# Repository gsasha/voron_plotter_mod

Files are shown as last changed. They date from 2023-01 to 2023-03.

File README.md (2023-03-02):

## Voron SB Plotter mod

###### Printing:
- Default voron settings, correct orientation
- No supports needed

###### Bom:
- 7 M3x8
- 7 M3 heatset inserts
- A very long M3 screw - including a long smooth part. 80mm is a good variant.
- A long spring. One harvested from a pen will be fine.
- 2 M3 washers
- MGW12C 100mm linear slide. Any other slide can be used, it's just one that was at hand.
- Sharpie pen.
- Vinyl cutter knife.

###### Description:
This is a plotter extension for Voron StealthBurner.
It uses a modified SB main body that includes two additional heatset inserts that the plotter attachment can be screwed to and removed easily.

The STLs supplied are tuned for MGW12C linear slide and regular Sharpie pen. However, most any slide and any pen can be used - LMK if you want STLs for different linear slides.

###### Assembly:

There are three printed parts: modified SB body, mounted plate and pen holder.

1. Print all the parts normally. The pen holder can be placed upside-down, this way it can be printed without supports. Otherwise, only the tab needs to be printed.

2. Install heatsets as indicated.
Pay especial attention to the plate - it is very important for alignment that the inserts are flush or even a bit deep.

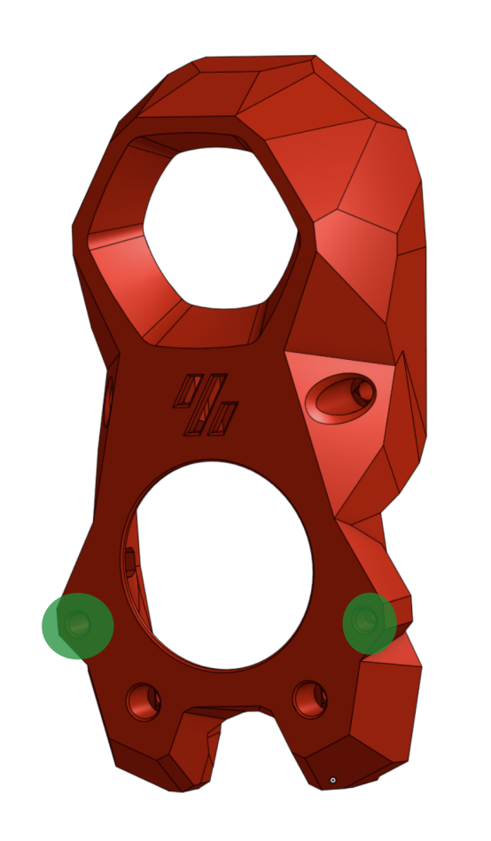
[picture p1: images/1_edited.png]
SB body
,
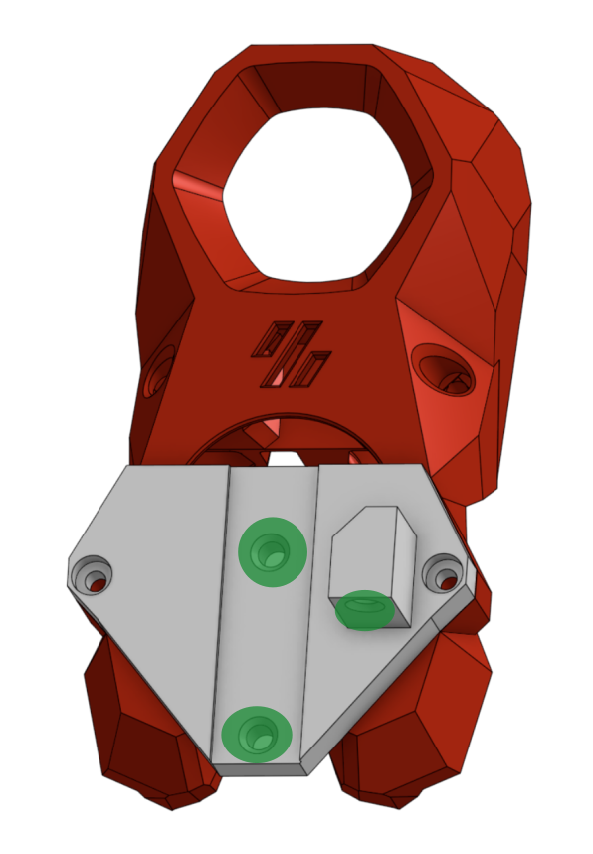
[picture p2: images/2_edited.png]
Plate
,
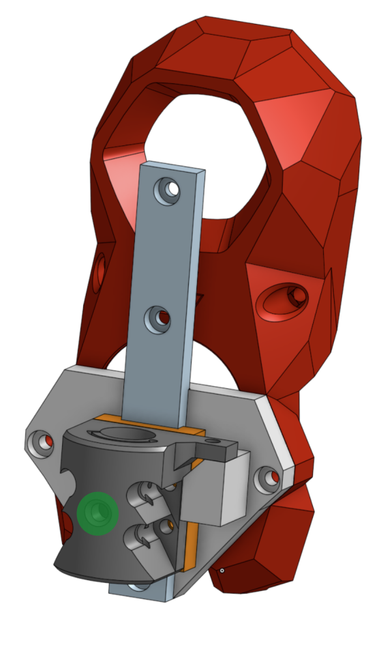
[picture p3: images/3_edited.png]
Pen Holder
.

3. Install the SB body onto the printer. The rest of the mechanism can be connected to it and disconnected again at will.

4. Screw the linear slide to the plate.

5. Screw the pen holder to the block.

6. Put a washer, a spring and another washer onto the long screw and screw it in from the top into the heatset insert on the limiter.

7. Insert a screw into the heatset in the pen holder.

###### Changing printer.cfg
Include the provider plot.cfg. Modify according to your printer (see comments inside).

###### Preparing Plotter file:

Plotter file must include `PLOT_START` as starter command.
For inkscape, copy the "inkscape/header" and "inkscape/footer" files to the directory where you put the output file.

Run the gcode through inkscape/preprocess.py to make it acceptable by klipper.

###### Running:

:warning: **!!!!! IMPORTANT !!!!!!** To prevent head crash, run the plotter with printer doors open.

Install the adapter (but not the pen) on the head. Run your generated gcode file.

The head should run the homing sequence and stop in the air. Install the pen so that it touches the bed, attach a page to be plotted using masking tape and unpause the printer.

##### Changelog:

**2 Mar 2023**:

- Added support for cutter knife.
- Knife and pen adapters are now interchangeable with less disassembly. In particular, the bolt holding the screw does not need to be removed.
- Small improvements to the structure to make it easier to print.
- Added location for nuts that can store mounting screws.

Enjoy!

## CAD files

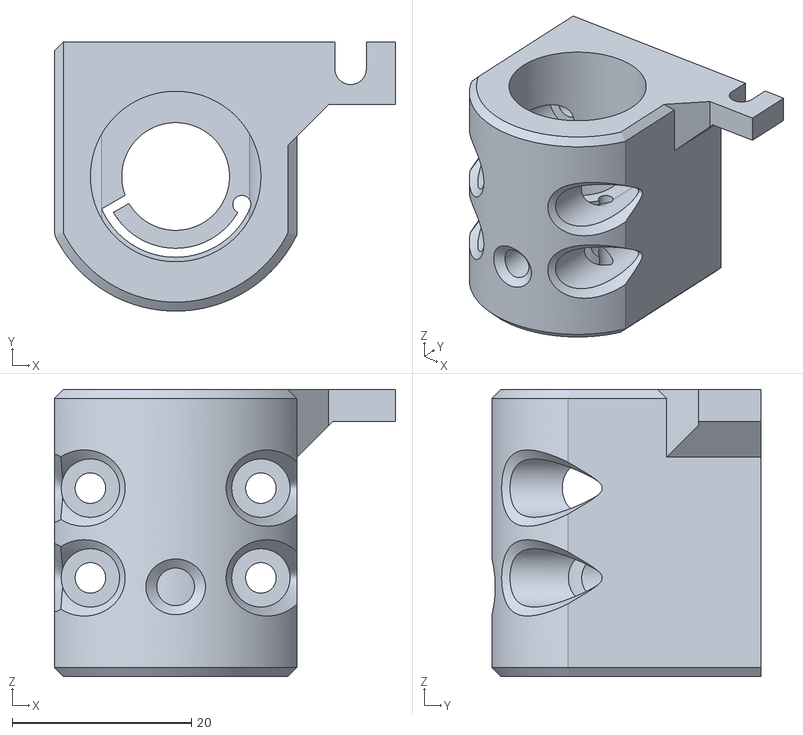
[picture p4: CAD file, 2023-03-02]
STL/mgw12c_holder_sharpie.stl
38.0 x 30.0 x 32.0

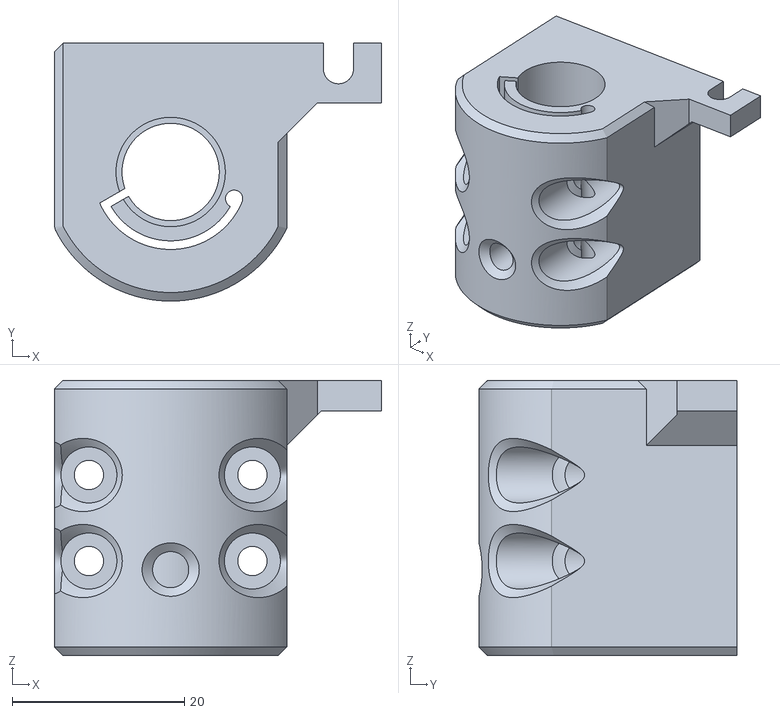
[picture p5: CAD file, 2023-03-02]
STL/mgw12c_holder_cutter.stl
38.0 x 30.0 x 32.0

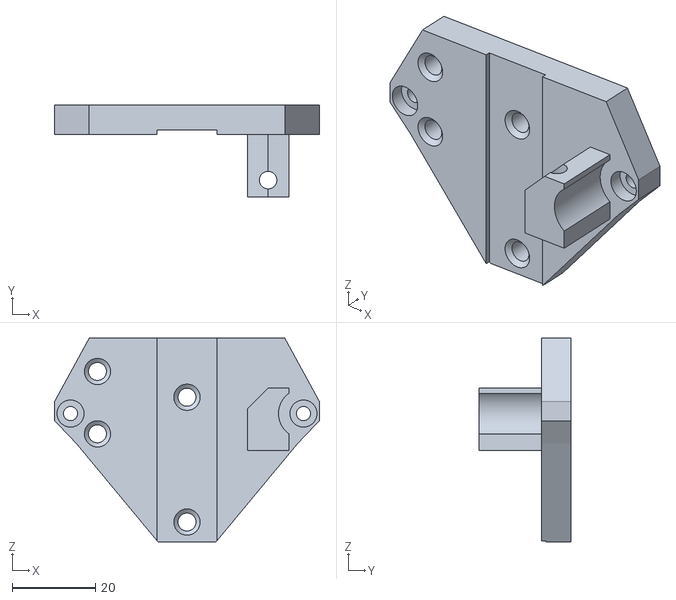
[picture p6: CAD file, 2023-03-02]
STL/mgw12c_plate.stl
63.7 x 22.0 x 48.9

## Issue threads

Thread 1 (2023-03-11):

On top of normal Stealthburner

14roiron, 2023-03-11:
Hello
Instead of reprinting a stealbruner top, I tried to modify your holder to be closer to the real one
I merged it with this one
https://github.com/DrPacemaker/Voron-Laser-Mod
but then support are required to print it, so it is not ideal
[plotter v1.stl.zip](https://github.com/gsasha/voron_plotter_mod/files/10948012/plotter.v1.stl.zip)

gsasha, 2023-03-12:
Nice!

Initially I tried this style of mount, but I decided that I don't like the
idea of disassembling the existing screws holding the SB faceplate.
Both have a right to exist, and I think we can try to make the mounts
compatible. WDYT?

An alternative way I'm thinking to implement this is to use a longer screw
permanently mounted in SB head with an adapter like this mounted on top of
it:
https://www.aliexpress.com/item/1005004157933737.html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,scm-url:1007.40050.281175.0,pvid:a579ff90-30bd-4b7a-bcaf-5242bfad5005,tpp_buckets:668%232846%238112%231997&isseo=y&pdp_ext_f=%7B%22sku_id%22%3A%2212000028233431605%22%2C%22sceneId%22%3A%2230050%22%7D&pdp_npi=3%40dis%21USD%213.0%212.82%21%21%21%21%21%40211b600e16786112126063788ea394%2112000028233431605%21rec%21IL%21171720285

Then, you can attach your extension to the adapter using a M5 nut. This is
not as fun as using an allen key, but still would be something that you can
attach to SB head without unscrewing it each time.

In the perfect world, we could find a stud like this:
https://www.aliexpress.com/item/1005003724900378.html?spm=a2g0o.detail.1000023.3.1a1d38bbBEsgR3
but with a very long thread and showt stud, it would allow mounting to the
stud easily. Alas, we're not in a perfect world...

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

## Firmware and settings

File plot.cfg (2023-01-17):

# Required to use inkscape-generated gcode.
[gcode_arcs]
# Required to have PAUSE and RESUME commmands.
[pause_resume]

[gcode_macro PLOT_START]
gcode:
    SET_FAN_SPEED FAN=light SPEED=1
    CLEAR_PAUSE
    BED_MESH_CLEAR
    G28
    # for Klicker or Euclid, pick up the probe.
    M401
    M117 QGL
    QUAD_GANTRY_LEVEL_ORIGINAL
    # No need for so much precision as to compute mesh.
    # Besides, printer is cold.
    # M117 Bed Mesh
    #respond msg="Bed Mesh"
    #BED_MESH_CALIBRATE_ORIGINAL
    M117 Auto Z
    CALIBRATE_Z
    # For Klicker or Euclid, park the probe.
    M402
    # Move the head to position where pen can be installed.
    G0 X30 Y60 Z10 F8000
    M117 Install pen
    # Mark the current position as 0, so that generated gcode will work.
    G92 X0 Y0 Z0
    # Wait for the user to install the pen and tell us that it's ready.
    PAUSE
 

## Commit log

2023-01-17 added plot.cfg
    [plot.cfg]
2023-03-02 added cutter
    [cutter_holder_mgw12c_sharpie.stl, pen_holder_mgw12c_sharpie.stl, plate_mgw12c.stl]
